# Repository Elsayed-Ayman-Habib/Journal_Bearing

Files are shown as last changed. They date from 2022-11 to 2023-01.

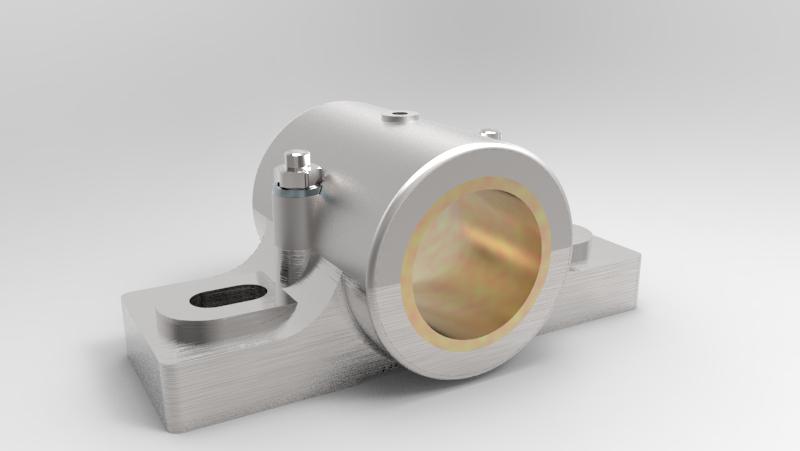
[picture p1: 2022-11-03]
Design/journal bearing.jpg

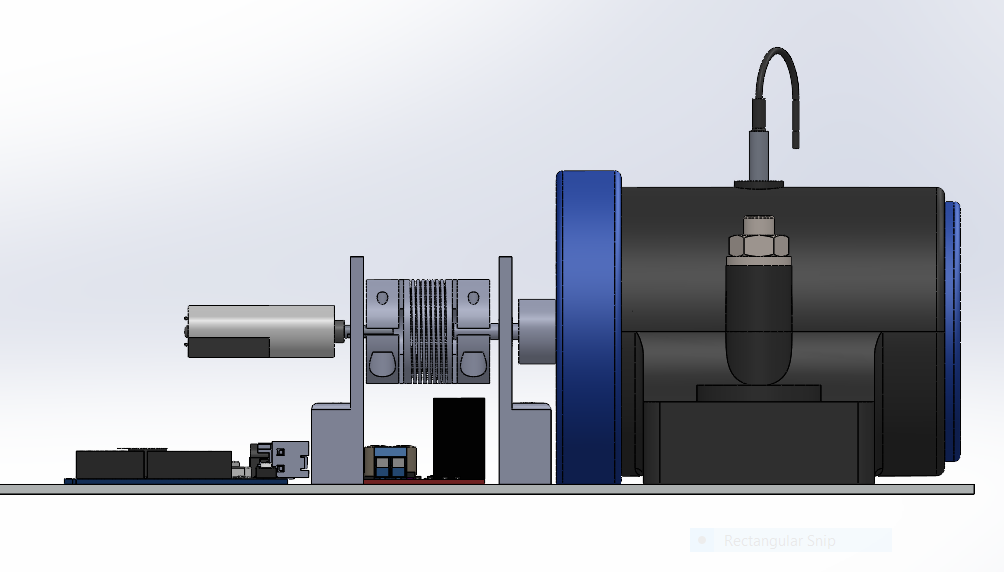
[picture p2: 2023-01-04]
First Picture.PNG

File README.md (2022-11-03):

# Journal_Bearing

Journal Bearings are widely used for lubrication, and are of great importance in many machines. During working conditions, the lubricant may reach unwanted temperatures due to friction and therefore lose its function and may lead to failure. In this project, we are required to design a journal bearing model and apply required control to prevent the lubricant used (oil) from reaching such temperatures.

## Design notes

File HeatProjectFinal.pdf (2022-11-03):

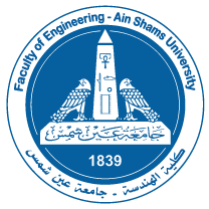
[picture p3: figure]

Faculty of Engineering
Ain Shams University
Senior Mechatronics Program Fall 2022

# MEP212: Heat Transfer

# Project 1

# TEAM 8

### Table of Contents

### Introduction

Journal Bearings are widely used for lubrication, and are of great importance in many machines. During working conditions, the lubricant may reach unwanted temperatures due to friction and therefore lose its function and may lead to failure. In this project, we are required to design a journal bearing model and apply required control to prevent the lubricant used (oil) from reaching such temperatures.

### Project Parts

1. 3D Printed Journal Bearing
2. Arduino Uno
3. DC Motor (12V 13000 RPM)
4. Motor Shaft + Coupler
5. L298N Motor Driver IC

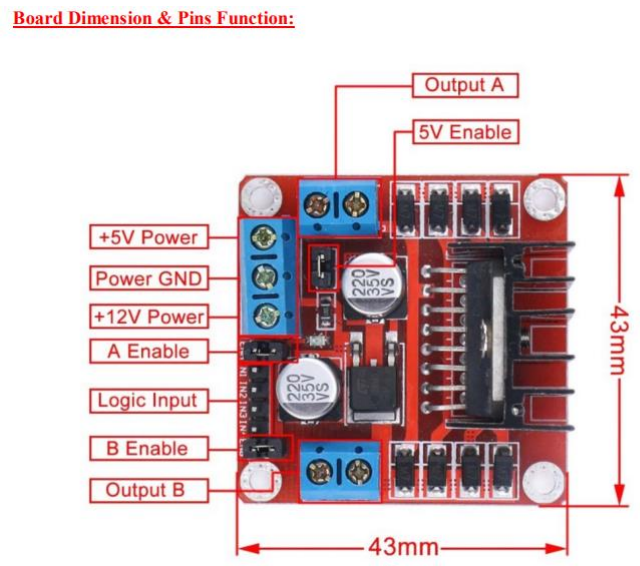
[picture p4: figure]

6. Temperature Sensor
7. LCD Screen
8. Breadboard + Wiring
9. Batteries
10. Oil (SAE 50 Dot 4 Brake Fluid)

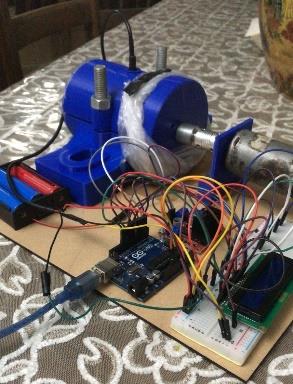
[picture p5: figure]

### Assembly Drawing

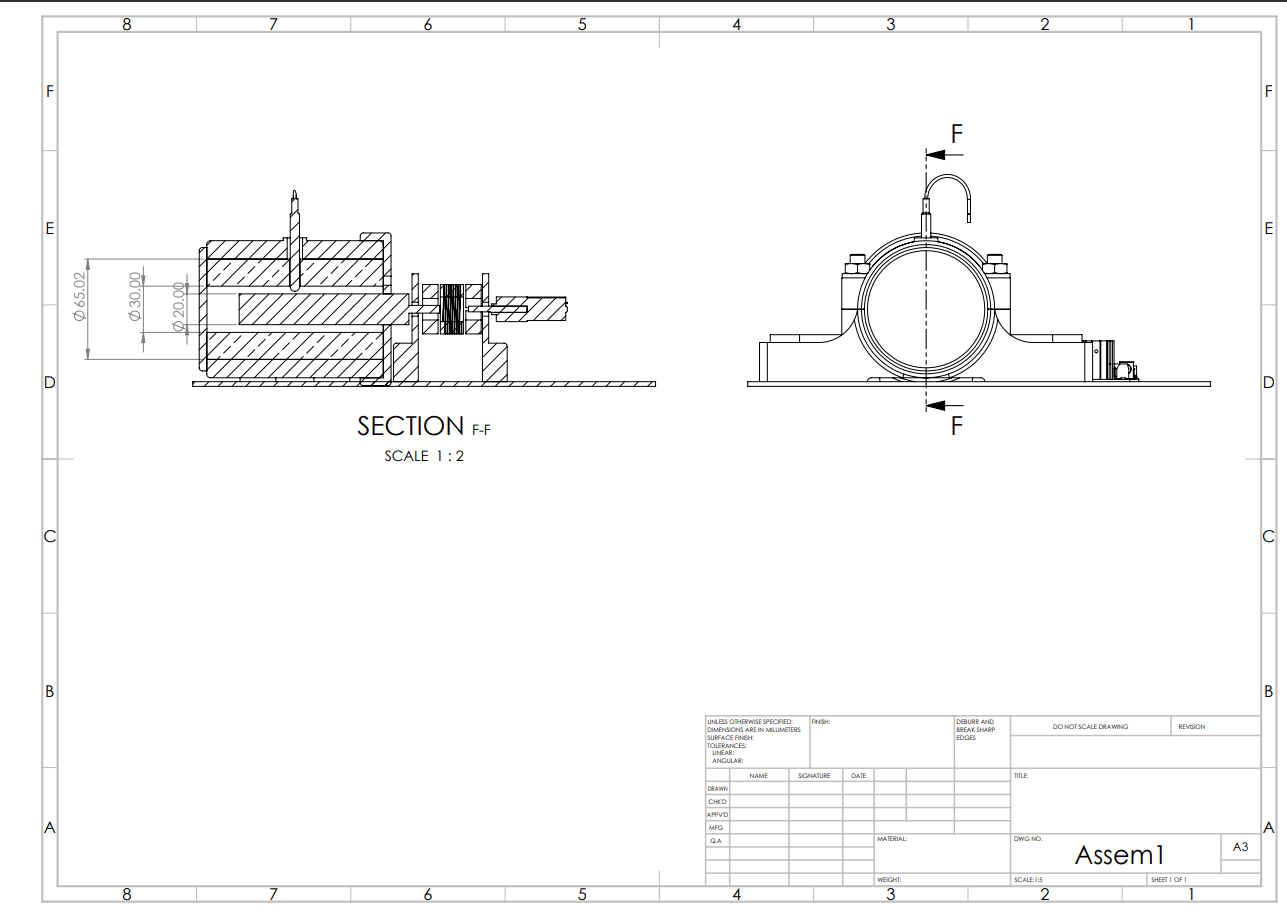
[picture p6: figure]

### Working Drawings

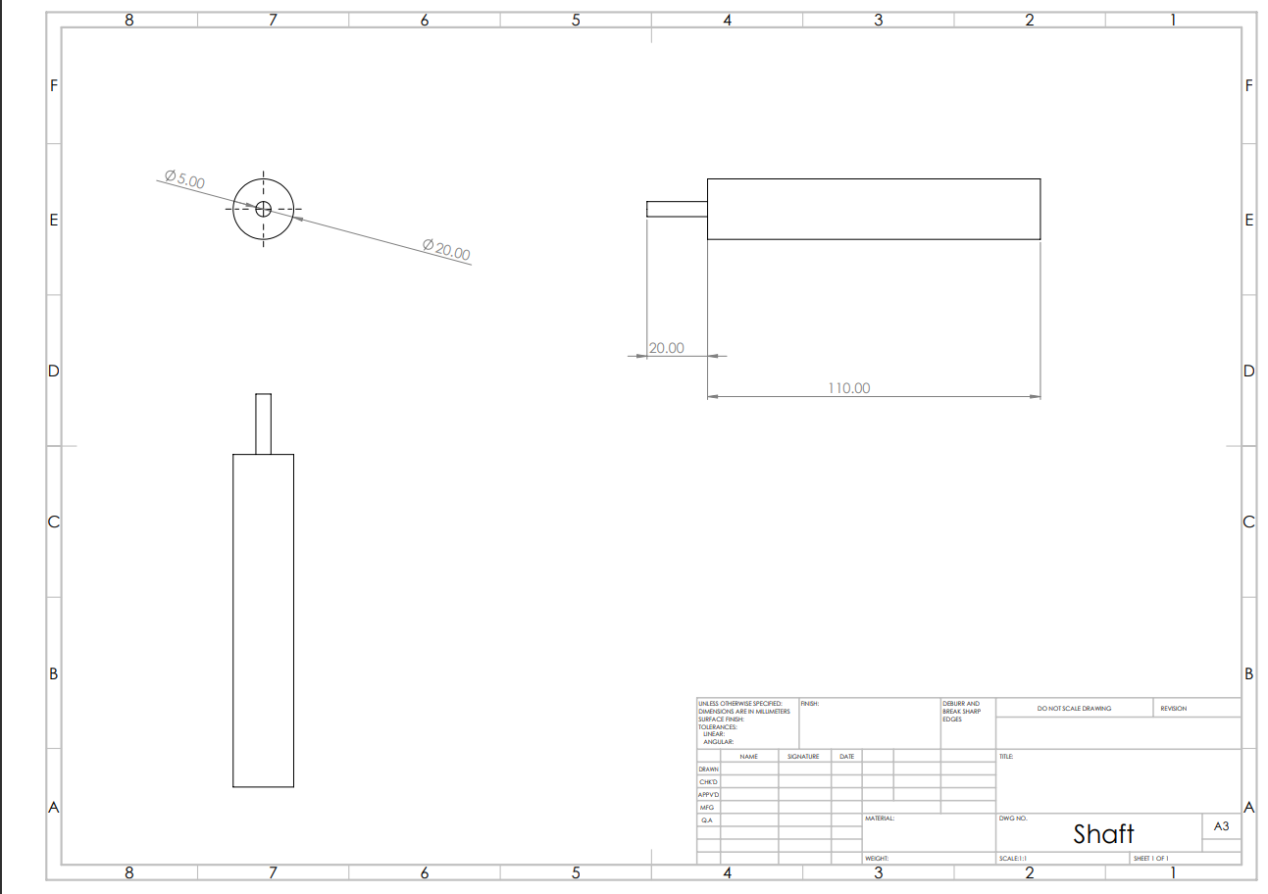
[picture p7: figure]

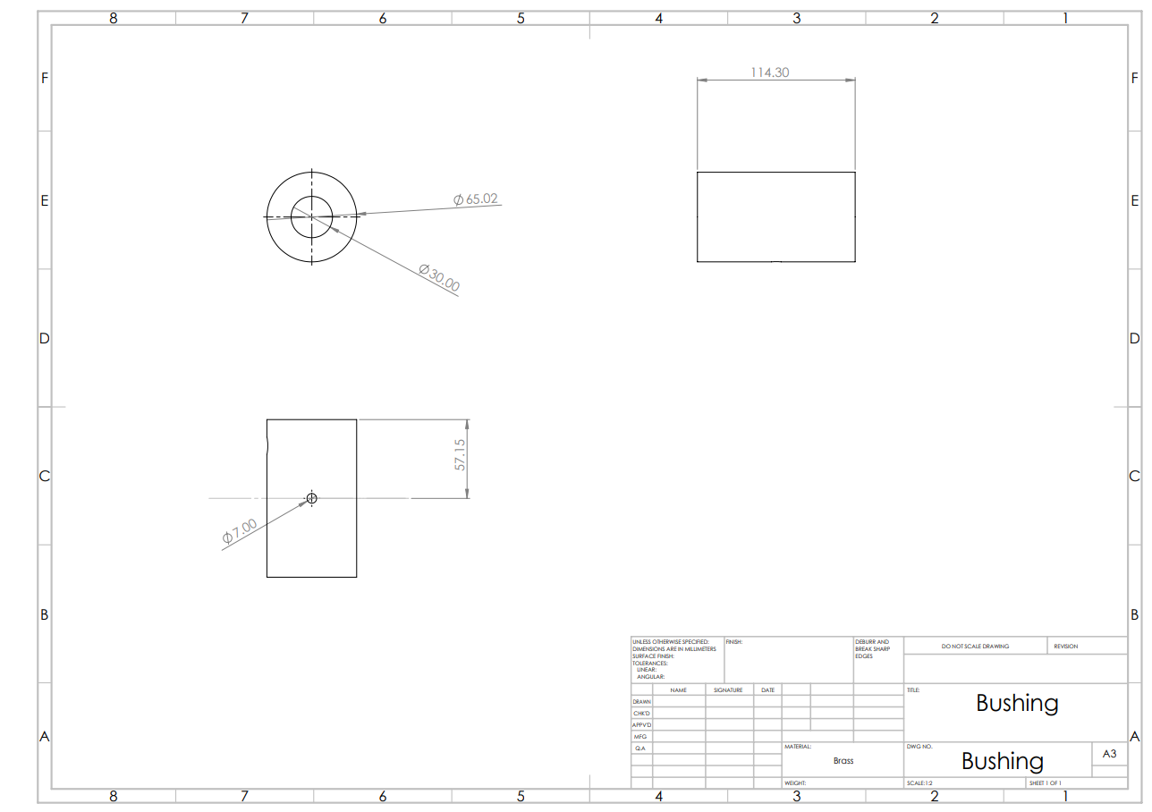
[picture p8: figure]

### Calculations

The flow of oil in a journal bearing can be approximated as parallel flow between two large plates with one plate moving and the other stationary. Such flows are known as Coutte flows. Consider two large isothermal plates separated by 5mm thick oil film.

- Assumptions

1- Steady operating conditions exist.

2- Oil is an incompressible substance with constant properties.

3- Body forces such as gravity are negligible.

4- The plates are large so that there is no variation in the z-direction.

-Givens

Shaft Diameter: d = 2cm = 1 × 10⁻²m

Properties of Dot 4 Brake Fluid SAE 50 at T0 = 25°C: k = 0.15 W/m.K

We can get the viscosity of the Oil at T0 = 25°C from the following graph and given values:

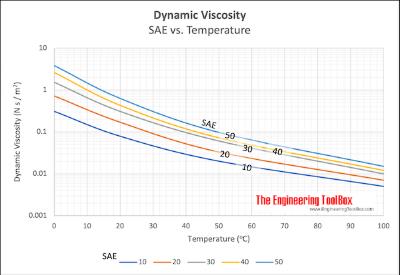
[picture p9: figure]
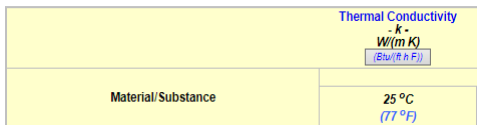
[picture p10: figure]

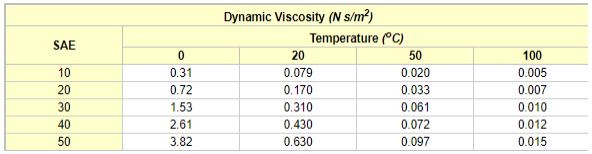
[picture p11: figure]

μ ≅ 0.6 Pa. s

-Proof

We take the x-axis to be the flow direction and y to be the normal direction. This is a parallel flow between two plates and thus v = 0. Then the continuity equation reduces to:

∂u
∂x +

∂v
∂y = 0 →

∂u
∂y = 0

∴ u = u(y)

Therefore, the x-component of velocity does not change in the flow direction (i.e. the velocity profile remains unchanged). Noting that u = u(y), v = 0 and ∂p
∂x= 0
(flow is maintained by the motion of upper plate rather than the x — momentum equation reduces to:

ρ (u

∂u
∂x + v

∂v
∂y) = μ

∂

2u
∂y² −

∂P
∂x

∴

∂

2u
∂y² = 0

This is a second order ordinary differential equation, by integrating twice gives:

u(y) = C1y + C2 the fluid velocities at the plate surfaces must be equal to velocities of the plates because of the no slip condition. Therefore, the boundary conditions are u(O) = 0 and u(L) = V and when applied gives the velocity distribution to be:

u(y) =

y
L

V

Frictional heating due to viscous dissipation in this case is significant because of the high viscosity of oil and the large plate velocity. The plates are isothermal and there is no charge in the flow direction and thus the temperature depends on y only T = T(y). Also u u(y) and v = O. Then the energy equation with dissipation reduce to:

ρCp (u

∂T
∂x + v

∂T

∂y) = K (
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
) + μφ

φ = 2 [(
∂u
∂x)

2
+ (

∂v
∂y)

2
] + (
∂u
∂y +

∂v
∂x)

2

∴ 0 = k

∂

2T
∂y

2 + μ (

∂u
∂y)

2

∴ k

∂

2T
∂y

2 = μ (

V
L

)

2

∂u
∂y =

V
L

Dividing both sides by k and integrating twice give:

T(y) =

μ
2k

(

y
L

V)

2
+ C3y + C4

Applying the boundary conditions:

T(O) = TO and T(L) = TO to give the temperature distribution:

T(y) = To +

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
The temperature gradient determined by differentiating T(y) with respect to y;

dT
dy =

μV

2
2kL (1 − 2

y
L

)

The location of maximum temperature is determined by setting dT/dy = 0 and solving for y:

dT
dy =

μV

2
2kL (1 − 2

y
L

) = 0

∴ y =

L
2
Therefore, maximum temperature at mid plane which is not surprising since both plates are maintained at the same temperatures the maximum temperature is given by:

Tmax = T (

L
2

) = TO + μV

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
Tmax = TO +

μV

2
8K

(Equation 1)

Heat flux at the plates is determined from the definition of heat flux:

q̇0 = −k

dT
dy |y=∞ = −k

μV

2
2kL (1 − 0) = −

μV

2
2L

(Equation 2)

-Experimental Values

From the Viscosity-Temperature graph of the oil, we can see that the viscosity reaches 0.1 Pa. s at almost 50°C ,so we can consider this to be Tmax.

From Equation 1:

V =

2πN
60 × r

50 = 25 +

0.6 × (

2πN
60 × 1 × 10⁻²
)

2

8 × 0.15
N = 6752.372 rpm

From Equation 2:

q̇0 = −

0.6 × (

2π × 6752.372
60 × 10⁻²

)

2

2(5 × 10⁻³)

= 3000 W/m²

To decrease Tmax by 20%, we can decrease the rpm to:

50(0.8) = 25 + 0.6 × ( | 2πN
| 60 × 1 × 10⁻²
)

2

| 8 × 0.15
N−20% = 5230.365 rpm

To increase Tmax by 10% and 20%, we repeat the previous step at Tmax = 50(1.1) and Tmax = 50(1.2) to get:

N+10% = 7396.85 rpm, N+20% = 7989.515 rpm

### Control Code

#include <LiquidCrystal.h>

#include <OneWire.h>

#include <DallasTemperature.h>

#define ONE_WIRE_BUS 7

/*ThermoCouple Pins*/

/**********************************/

OneWire oneWire(ONE_WIRE_BUS);

DallasTemperature sensors(&oneWire);

float Celcius = 0;

/*********************************/

/*LCD Pins*/

const int rs = 12, en = 11, d4 = 5, d5 = 4, d6 = 1, d7 = 2;

LiquidCrystal lcd(12, 11, 5, 4, 1, 2);

/*************************************/

/*Bridge Pins*/

const int pwm = 3 ; //initializing pin 3 as pwm

const int in_1 = 8 ;

const int in_2 = 9 ;

/*********************/

void setup()

{

sensors.begin();

lcd.begin(16, 2);

lcd.clear();

pinMode(10, OUTPUT);

analogWrite(10, 0);

pinMode(in_1, OUTPUT);

pinMode(in_2, OUTPUT);

Serial.begin(9600);

}

void loop()

{

sensors.requestTemperatures();

Celcius=sensors.getTempCByIndex(0);

lcd.setCursor(0, 0);

lcd.print("Temp = ");

lcd.setCursor(10, 0);

lcd.print(Celcius);

delay(1000);

/*digitalWrite(in_1,HIGH) ;

digitalWrite(in_2,LOW) ;

analogWrite(pwm,255) ;*/

Serial.print(Celcius);

Serial.print("\n");

lcd.setCursor(0, 0);

lcd.print("Temp = ");

lcd.print(Celcius);

if(Celcius >= 45 )

{

digitalWrite(in_1,LOW) ;

digitalWrite(in_2,LOW) ;

}

else if(Celcius < 45 || Celcius >= 25 )

{

digitalWrite(in_1,HIGH) ;

digitalWrite(in_2,LOW) ;

analogWrite(pwm,125) ;

}

else if( Celcius < 25)

{

digitalWrite(in_1,HIGH) ;

digitalWrite(in_2,LOW) ;

analogWrite(pwm,255) ;

}

}

### Circuit Connection

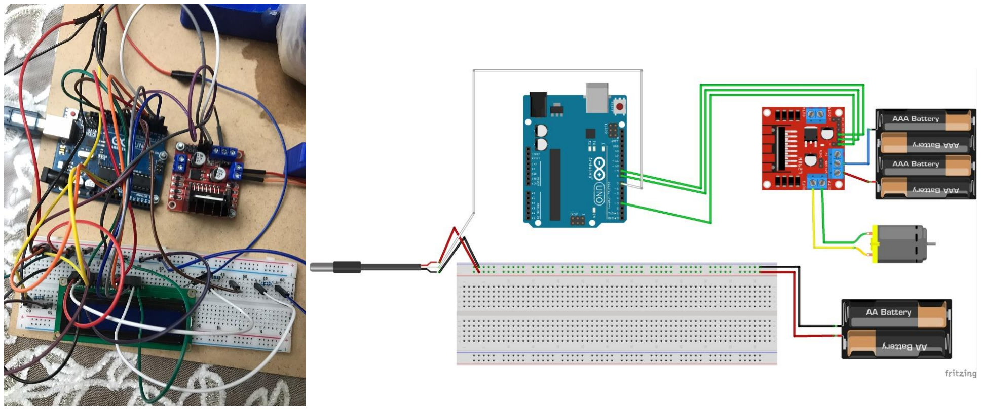
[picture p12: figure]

### Conclusion

Using this method, we were able to control the system to prevent any potential failure.

### References

1) https://www.engineeringtoolbox.com/dynamic-viscosity-motor-oils-d_1759.html (https://www.engineeringtoolbox.com/dynamic-viscosity-motor-oils-d_1759.html)
2) https://www.engineeringtoolbox.com/thermal-conductivity-d_429.html
3) http://www.handsontec.com/dataspecs/L298N%20Motor%20Driver.pdf

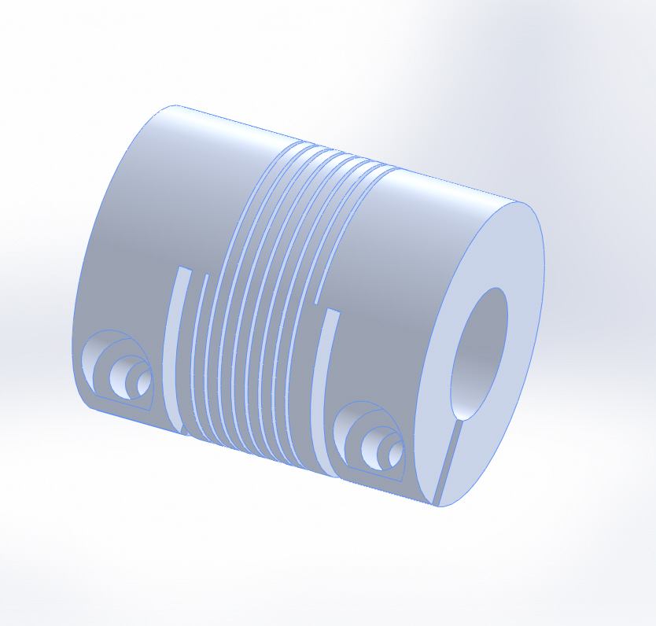
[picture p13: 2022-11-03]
Design/Flexible Coupling 1.JPG

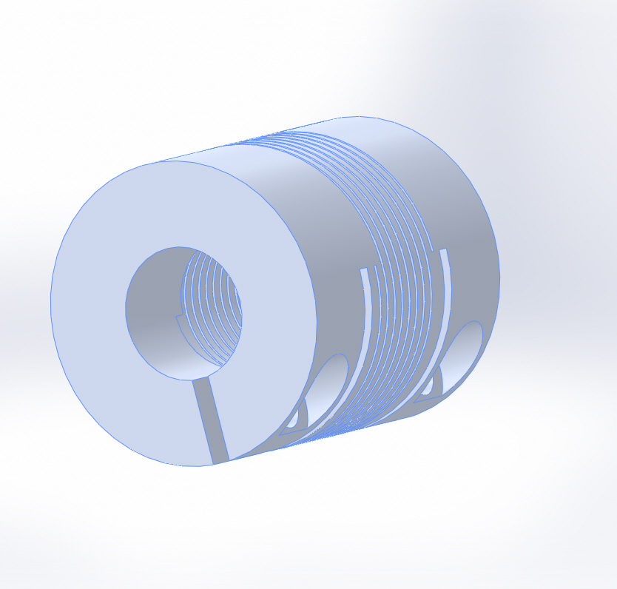
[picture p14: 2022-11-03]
Design/Flexible Coupling 2.JPG

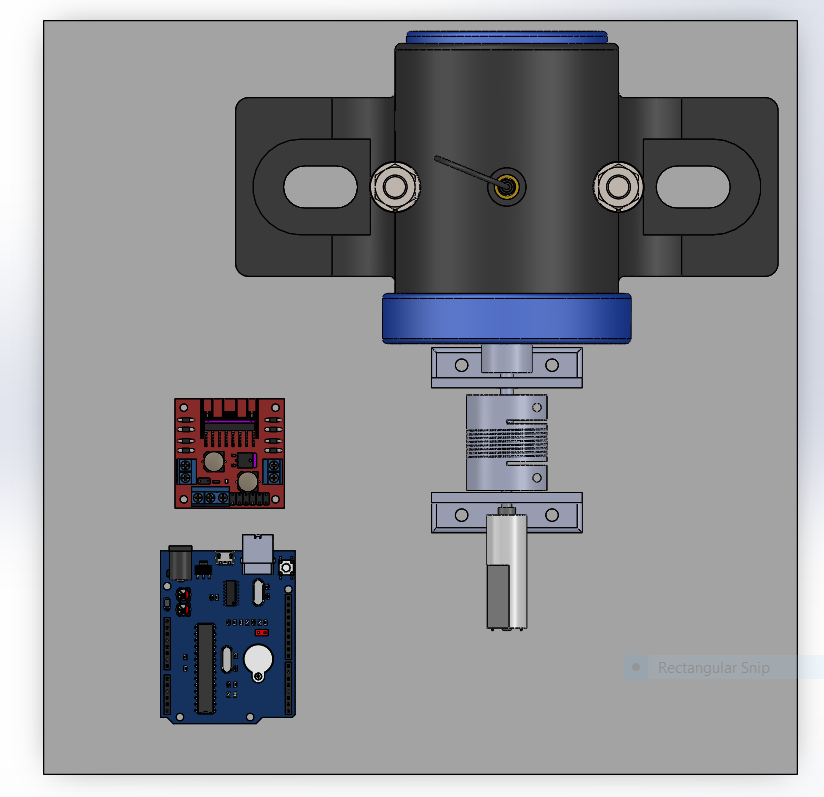
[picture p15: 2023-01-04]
Third Picture.PNG

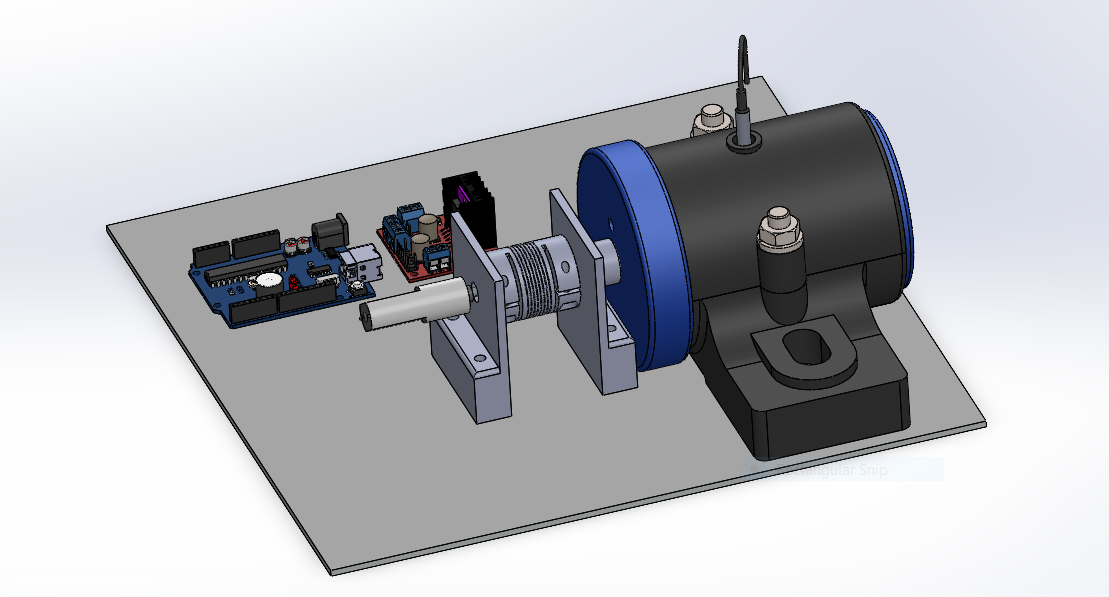
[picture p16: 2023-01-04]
Second Picture.PNG

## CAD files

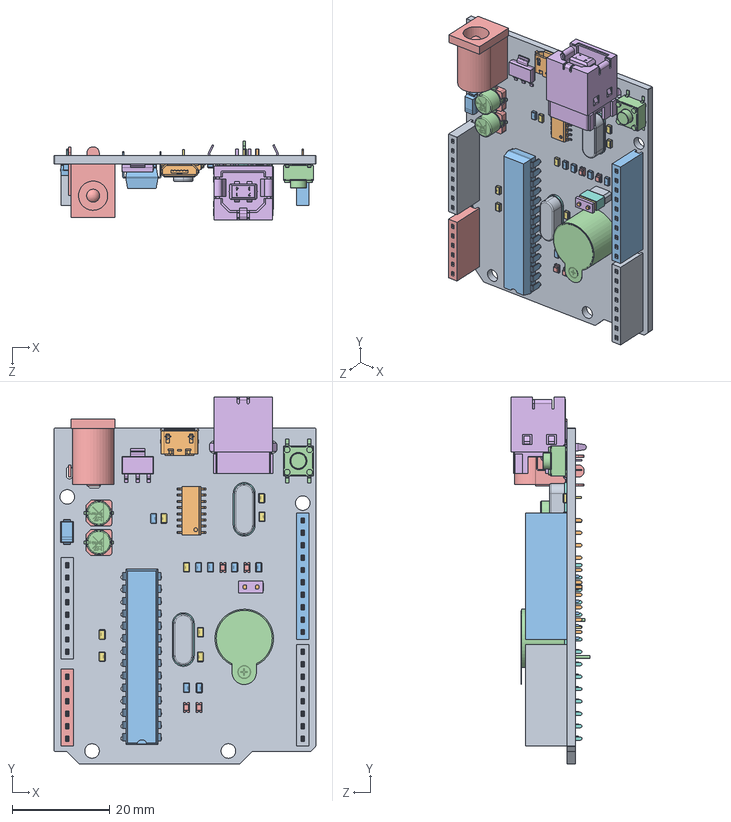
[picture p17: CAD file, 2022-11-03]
Design/New folder/UNO_PCB.SLDASM
53.6 x 75.2 x 16.2 mm
Micro_USB
SW3dPS-0805_SMD_Resistor x 7
User_Library-Buzzer_WST-1203UX
User_Library-led_0805-blue x 4
Extruded
Extruded_2
Extruded_3
Extruded_4
Extruded_5 x 2
User_Library-DO-214Aa_SMA
capicitor_5x5.5x1.4 x 2
Base___X2__03A6__X0__5Capacitor x 2
SW3DPS-SOT-223-DEFAULT
User_Library-HC49S-1_Fusion x 2
User_Library-HC49S-1_Fillet x 2
User_Library-HC49S-1_Fillet002 x 2
User_Library-SOIC-16-1
SW3dPS-DIP28-300
4301x20508x6
SW3dPS-dc_range_-_dc_connector[4840.2201]
c-0292304-01-b-3d
0805_SMD_Capacitor x 8
6130xx11821_PIN x 16
6130xx11821_PIN_2 x 10
6130xx11821_PIN_3 x 6

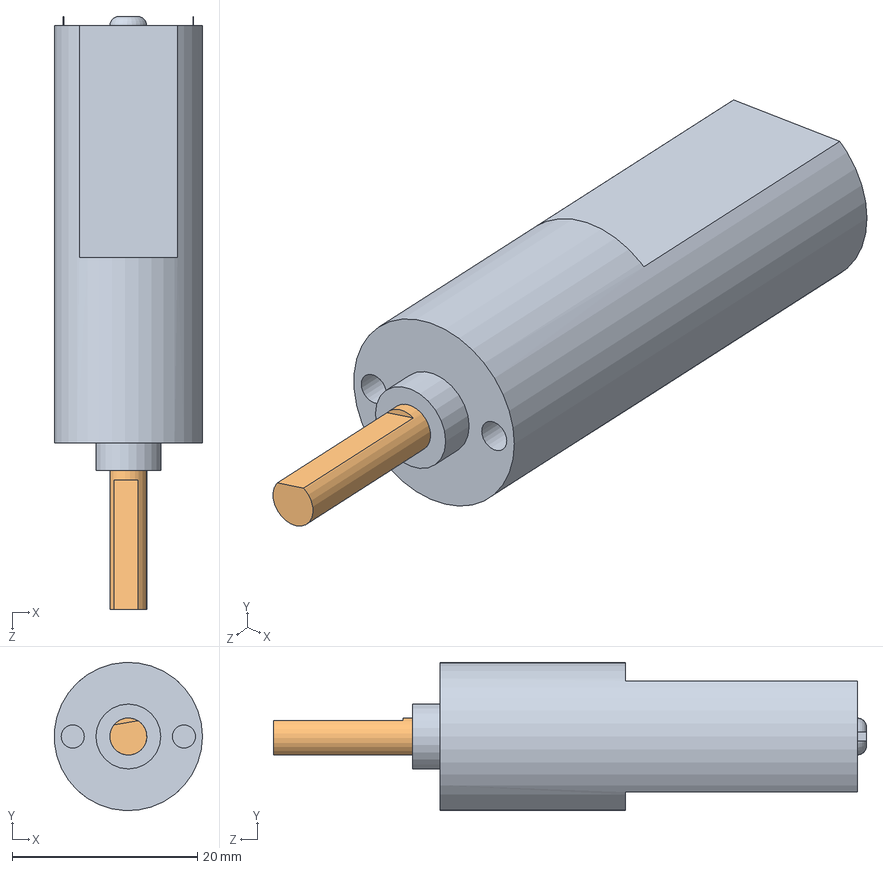
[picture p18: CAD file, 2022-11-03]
Design/New folder/DCMotor12V.SLDASM
16.0 x 16.0 x 64.0 mm
DCBody
mil

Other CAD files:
Design/Jump.SLDASM
Design/R2.SLDASM
Design/UNO_PCB.SLDASM
Design/DIO1.SLDASM
Design/Reset.SLDASM
Design/C4.SLDASM
Design/Cx8.SLDASM
Design/USB_2.SLDASM
Design/Cx4.SLDASM
Design/X2.SLDASM
Design/6-20V_DC.SLDASM
Design/CH340G.SLDASM
Design/R3.SLDASM
Design/X1.SLDASM
Design/Cx5.SLDASM
Design/Cx2.SLDASM
Design/0805_SMD_Capacitor.SLDPRT
Design/4301x20508x6.SLDPRT
Design/5x5.5x1.4.SLDASM
Design/61300611821.SLDASM
Design/61300611821.SLDPRT
Design/61300811821.SLDASM
Design/61300811821.SLDPRT
Design/61301011821.SLDASM
Design/61301011821.SLDPRT
Design/6130xx11821_PIN.SLDPRT
Design/6130xx11821_PIN_2.SLDPRT
Design/6130xx11821_PIN_3.SLDPRT
Design/8020055440.SLDASM
Design/8020055600.SLDASM
Design/8020055840.SLDASM
Design/8020056160.SLDASM
Design/8020056400.SLDASM
Design/AMS1117.SLDASM
Design/ATmega328p.SLDASM
Design/Assem1.SLDASM
Design/Assem1.SLDDRW
Design/Base___X2__03A6__X0__5Capacitor.SLDPRT
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

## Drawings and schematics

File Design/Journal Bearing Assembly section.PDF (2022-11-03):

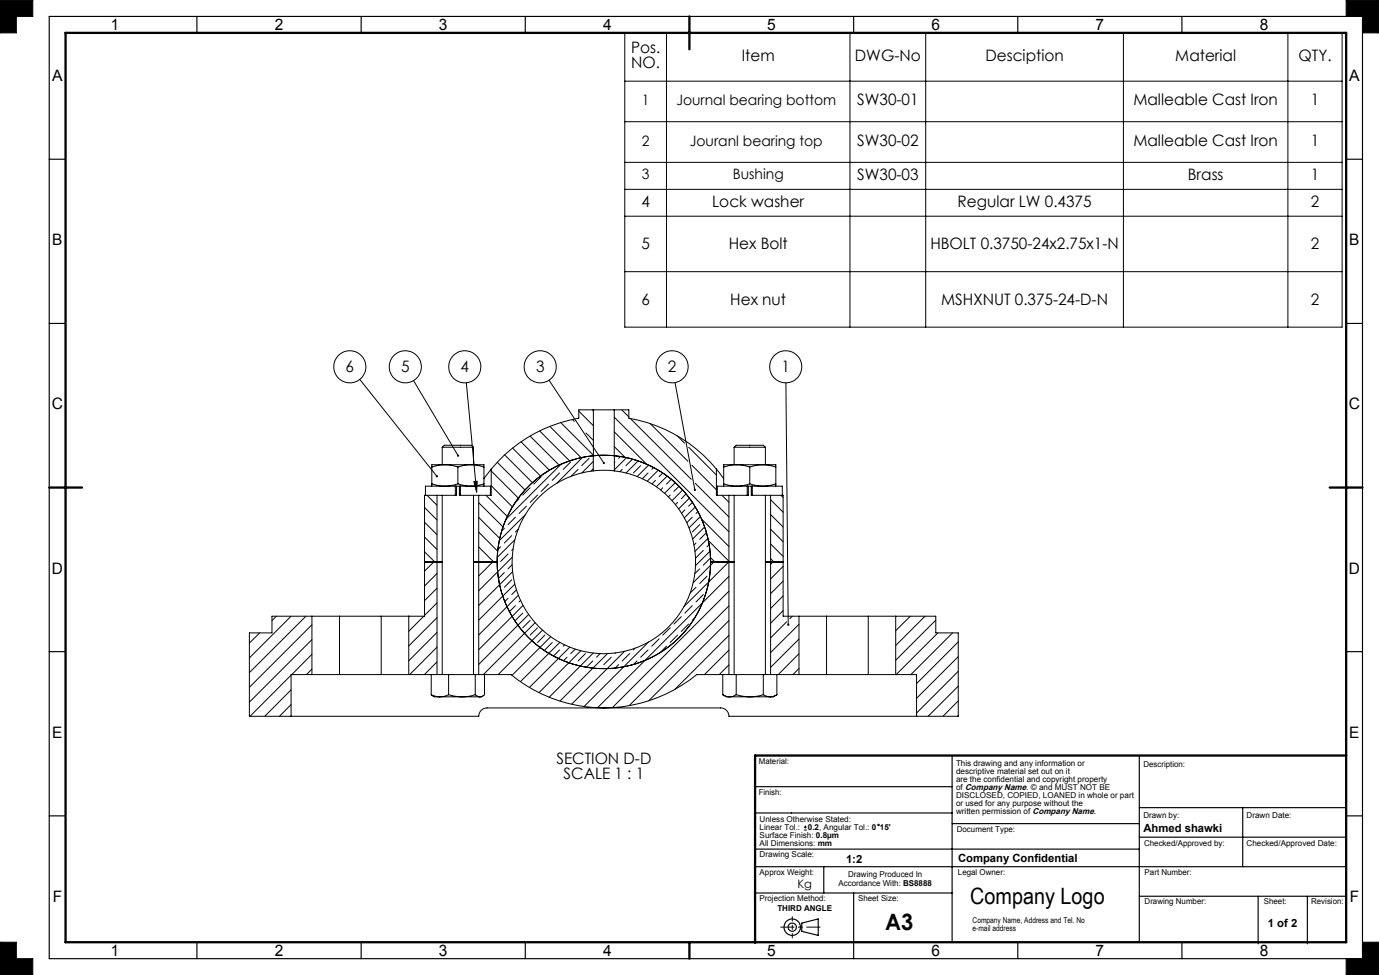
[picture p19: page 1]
SECTION D-D SCALE 1 : 1; Document Type:; Ahmed shawki; Drawing Scale:; Company Confidential; Drawn by:; Projection Method:; Sheet Size:; THIRD ANGLE; Approx Weight:; Legal Owner:; Drawing Number:; Sheet:; Revision:; Part Number:; Company Logo

Pos. NO. | Item | DWG-No | Desciption | Material | QTY.

1 | Journal bearing bottom | SW30-01 | | Malleable Cast Iron | 1
2 | Jouranl bearing top | SW30-02 | | Malleable Cast Iron | 1
3 | Bushing | SW30-03 | | Brass | 1
4 | Lock washer | | Regular LW 0.4375 | | 2

5 | Hex Bolt | | HBOLT 0.3750-24x2.75x1-N | | 2

6 | Hex nut | | MSHXNUT 0.375-24-D-N | | 2

This drawing and any information or
descriptive material set out on it
are the confidential and copyright property
of Company Name. © and MUST NOT BE
DISCLOSED, COPIED, LOANED in whole or part
or used for any purpose without the
written permission of Company Name.

Drawn Date: Unless Otherwise Stated:
Linear Tol.: 0.2, Angular Tol.: 0 15'
Surface Finish: 0.8µm
All Dimensions: mm

Checked/Approved by:

Checked/Approved Date:

Drawing Produced In
Accordance With: BS8888

Company Name, Address and Tel. No
e-mail address

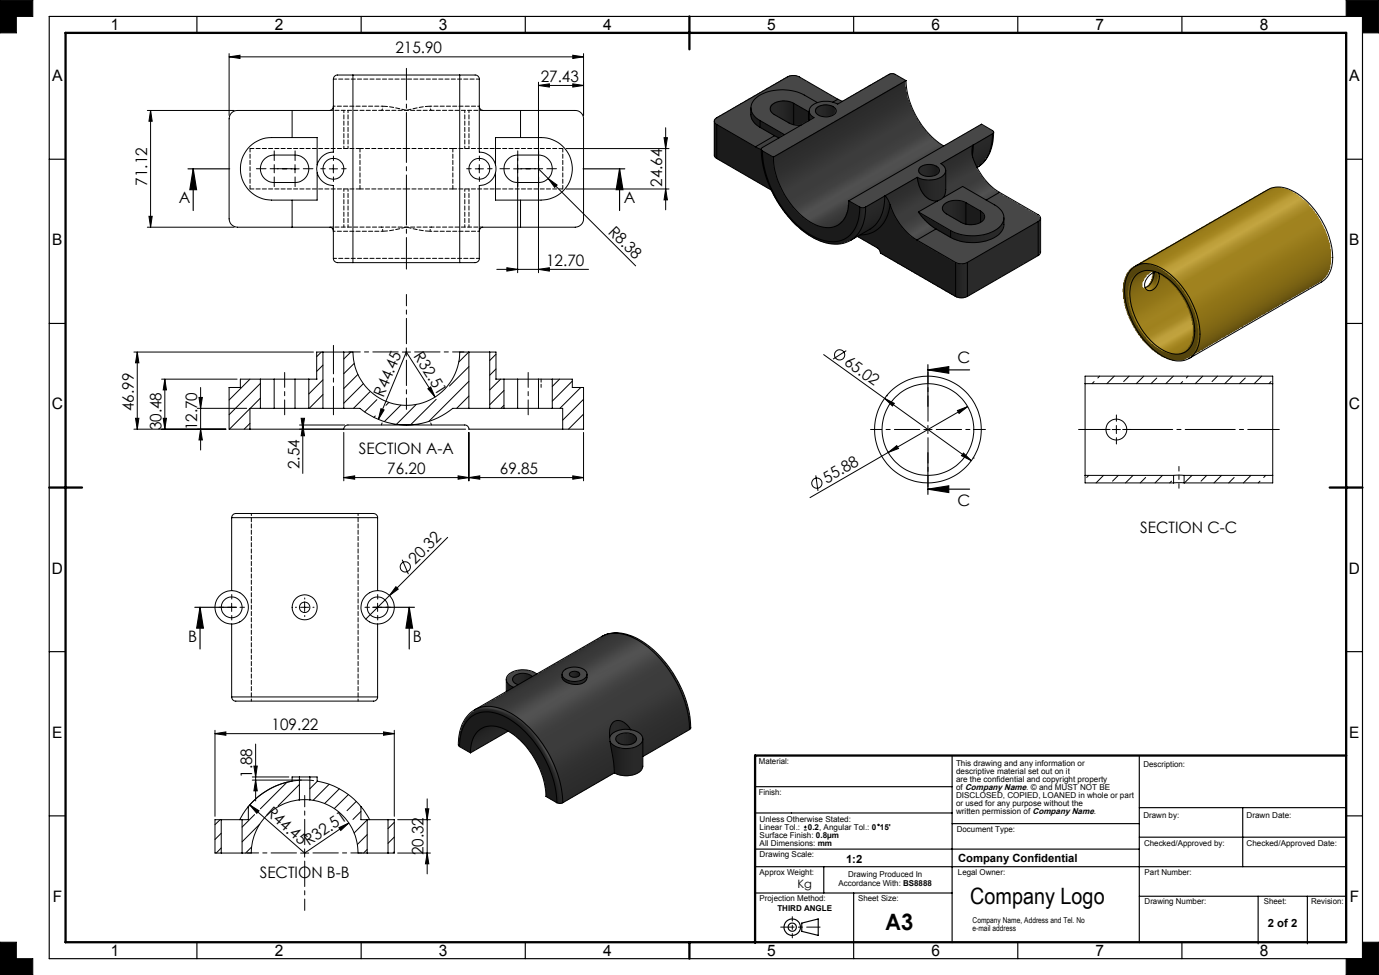
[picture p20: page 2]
SECTION A-A; SECTION B-B; SECTION C-C; Drawing Scale:; Company Confidential; Drawn by:; Projection Method:; Sheet Size:; THIRD ANGLE; Approx Weight:; Legal Owner:; Drawing Number:; Sheet:; Revision:; Part Number:

This drawing and any information or
descriptive material set out on it
are the confidential and copyright property
of Company Name. © and MUST NOT BE
DISCLOSED, COPIED, LOANED in whole or part
or used for any purpose without the
written permission of Company Name.
Document Type:
Company Logo

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

Checked/Approved by:

Checked/Approved Date:

Drawing Produced In
Accordance With: BS8888

Company Name, Address and Tel. No
e-mail address

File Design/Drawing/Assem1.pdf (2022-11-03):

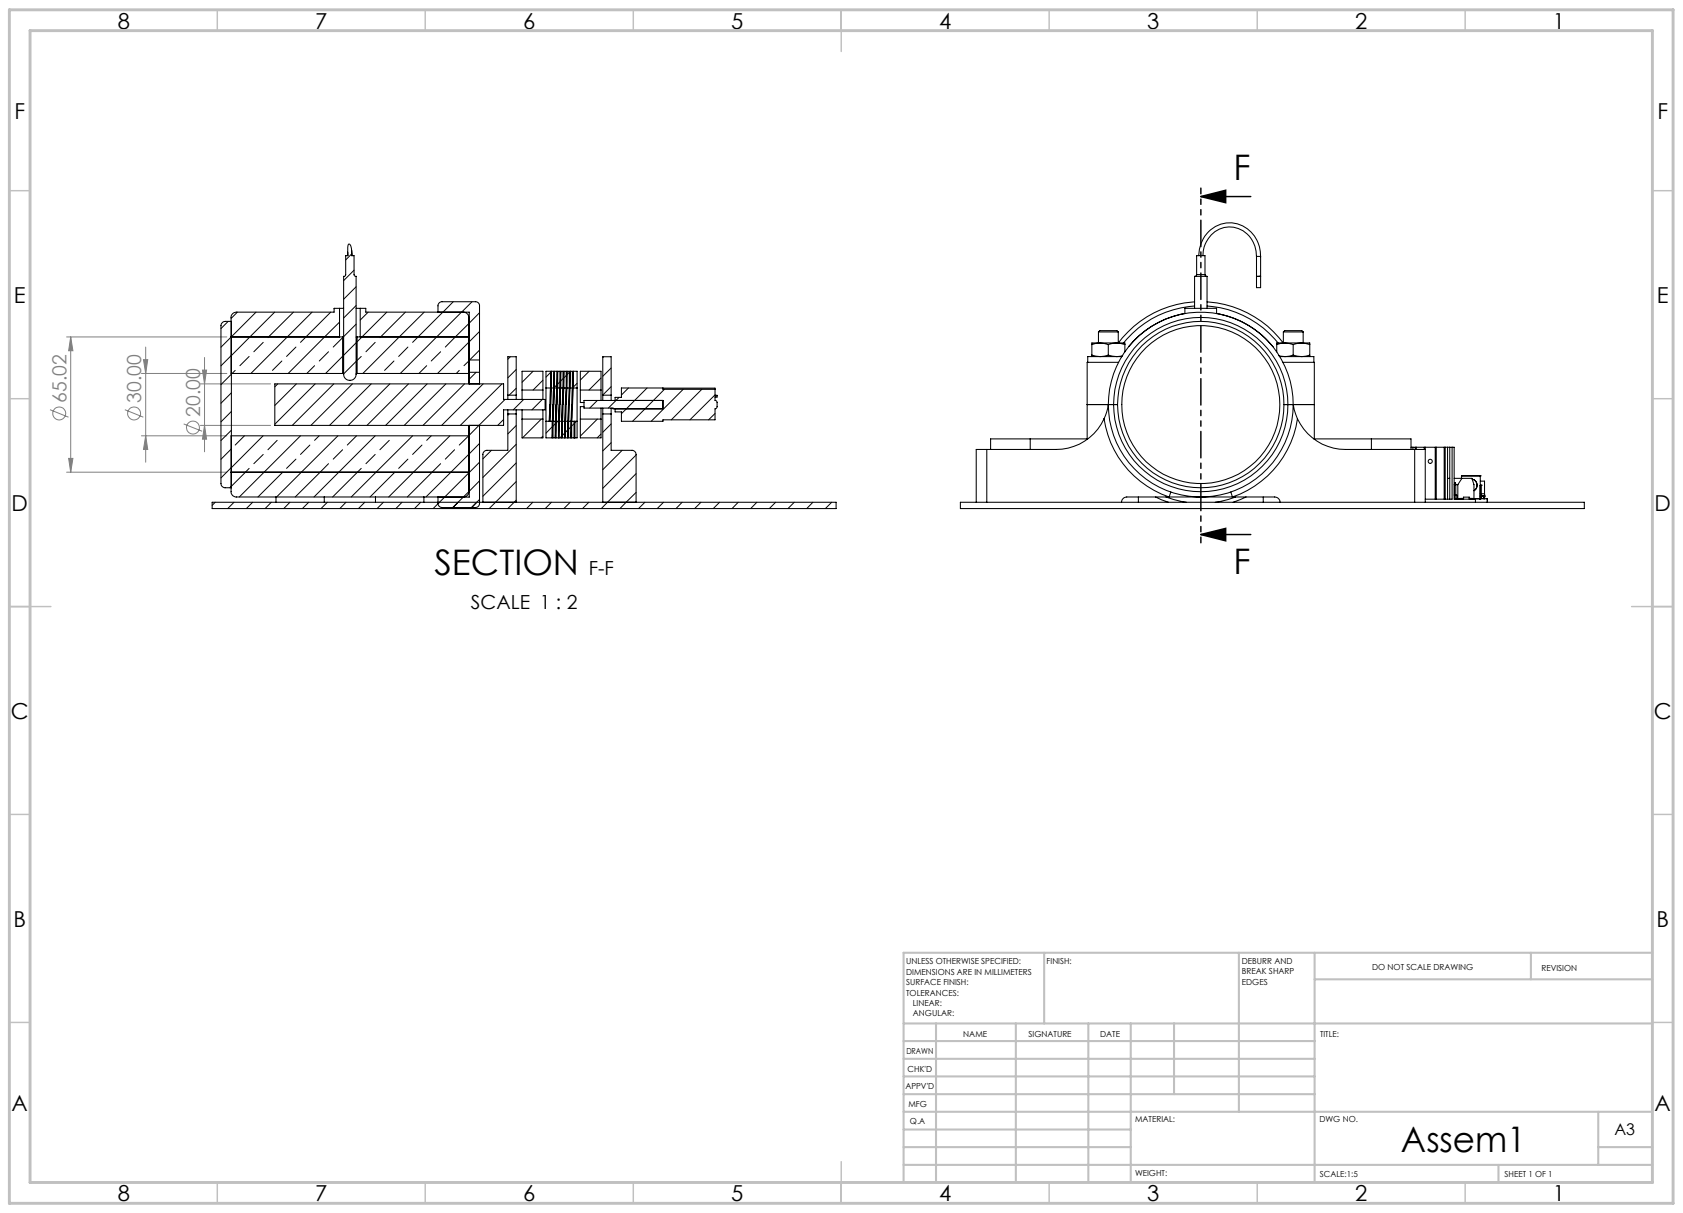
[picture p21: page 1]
SECTION F-F; SCALE 1 : 2; FINISH:; DEBURR AND; BREAK SHARP; DO NOT SCALE DRAWING; REVISION; SCALE:1:5; SHEET 1 OF 1

UNLESS OTHERWISE SPECIFIED:
DIMENSIONS ARE IN MILLIMETERS
SURFACE FINISH:
TOLERANCES:
LINEAR:
ANGULAR:

NAME | SIGNATURE | DATE | | | | TITLE:

DRAWN
CHK'D
APPV'D
MFG
Q.A | | | | MATERIAL: | DWG NO. Assem1 | A3

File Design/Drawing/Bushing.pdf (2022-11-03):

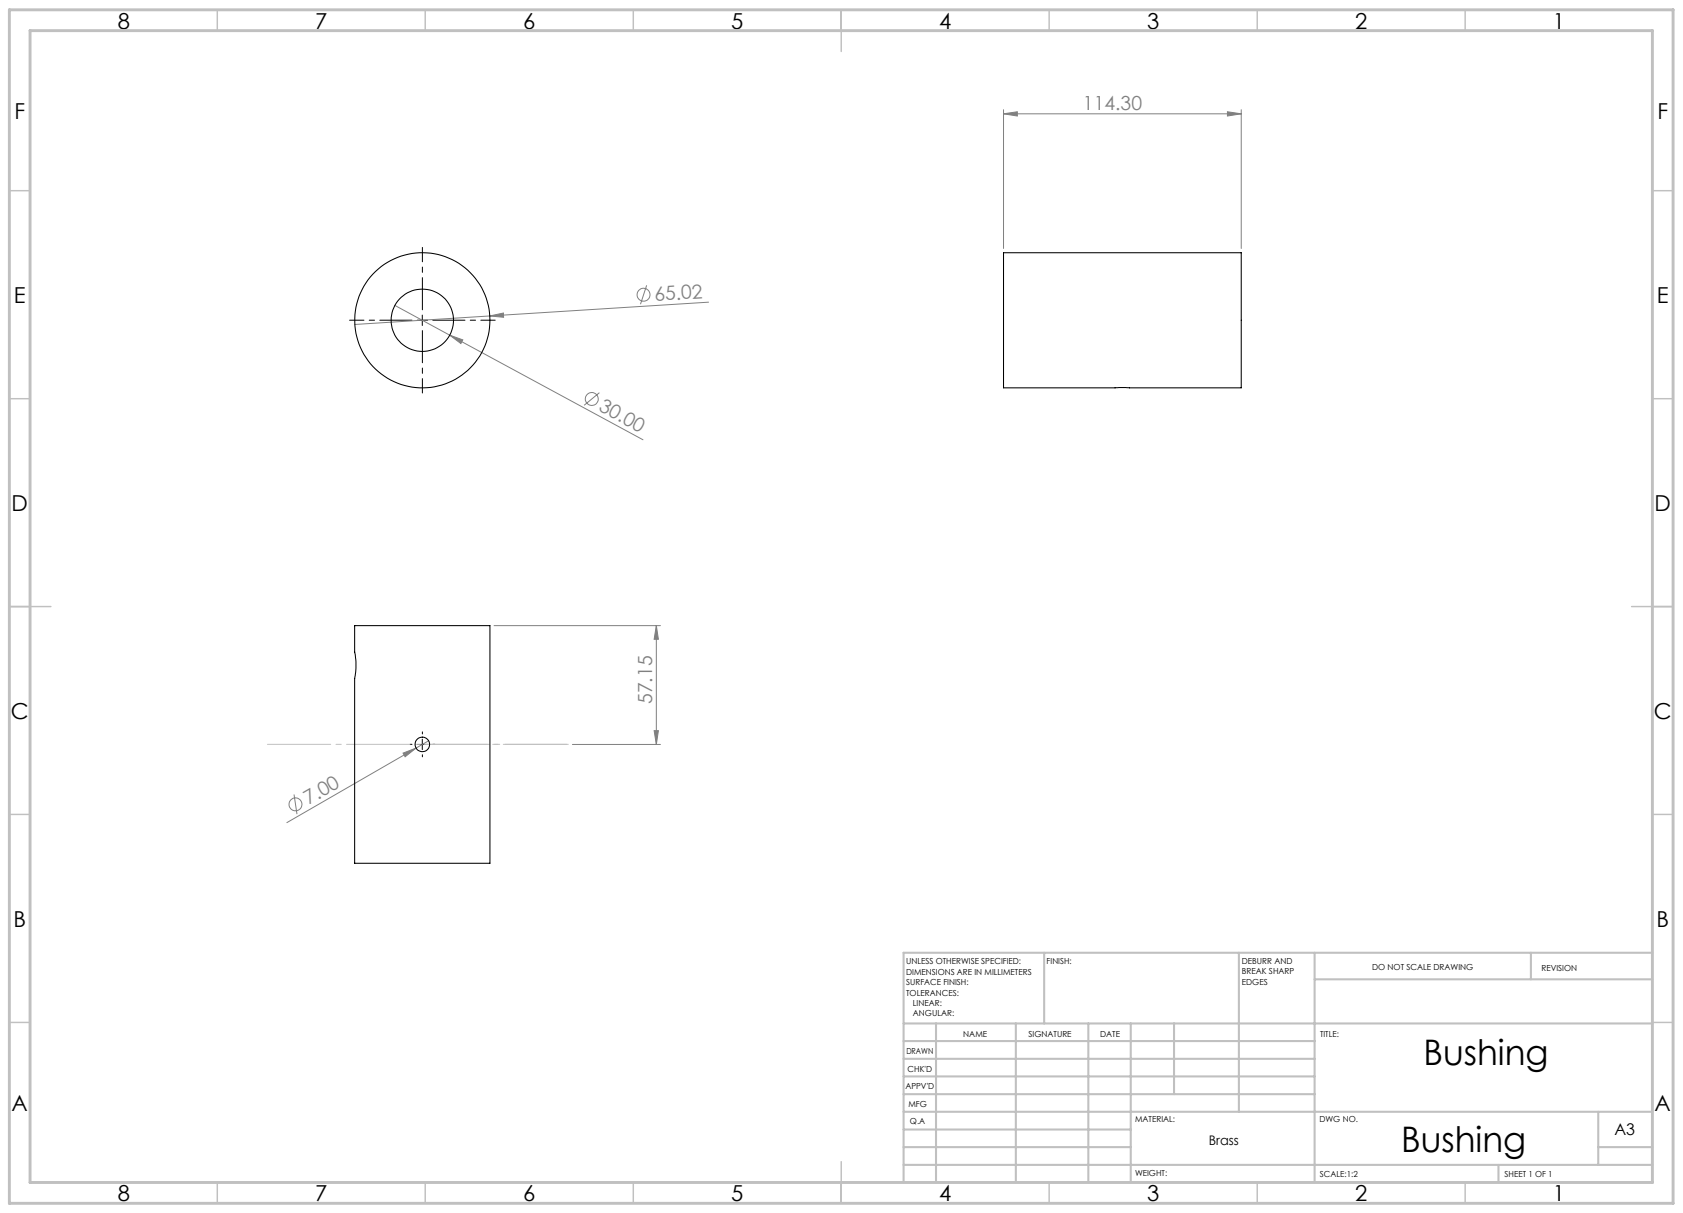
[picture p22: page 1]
FINISH:; DEBURR AND; BREAK SHARP; DO NOT SCALE DRAWING; REVISION; SCALE:1:2; SHEET 1 OF 1

UNLESS OTHERWISE SPECIFIED:
DIMENSIONS ARE IN MILLIMETERS
SURFACE FINISH:
TOLERANCES:
LINEAR:
ANGULAR:

NAME | SIGNATURE | DATE | | | | TITLE: Bushing

DRAWN
CHK'D
APPV'D
MFG
Q.A | | | | MATERIAL: Brass | DWG NO. Bushing | A3

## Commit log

2022-11-03 Journal Bearing (Heat Transfer)
    [0805_SMD_Capacitor.SLDPRT, 4301x20508x6.SLDPRT, 5x5.5x1.4.SLDASM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]
2023-01-04 Pictures of assembly
